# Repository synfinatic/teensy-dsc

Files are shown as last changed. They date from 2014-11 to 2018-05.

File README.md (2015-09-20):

# TeensyDSC: WiFi enabled Digital Setting Circles

## Important Note

As of Nov 16, 2014 I've been able to order a PCB from OSHPark using the 
[Simple-DSC](https://github.com/synfinatic/teensy-dsc/tree/simple-dsc/eagle)
design and with the latest code from 
[master](https://github.com/synfinatic/teensy-dsc/commit/1c4c6b0b567ba3cc21cd7ba83029384eee6130e7).
I seem to have a working solution using SkySafari Pro on my iPad with 
[US Digital S2-2500](http://www.usdigital.com/products/encoders/incremental/rotary/shaft/S2)
10,000 step optical encoders.

For more information, please see the [TeensyDSC Wiki](https://github.com/synfinatic/teensy-dsc/wiki)

There is also this thread on [CloudyNights](http://www.cloudynights.com/topic/482436-yet-another-diy-digital-setting-circles-project-teensydsc/)

## Basic Features
I wanted to do my own digital setting circles (DSC) for my 
[Apertura AD12](http://www.opticsmart.com/telescopes/dobsonian-telescopes/apertura-ad12-dobsonian-reflector-telescope.html).
The main goals were:

 * Tested to support 40,000 resolution via quadurature decoding using [US Digital S2-10000-250-IE-D-D encoders](http://usdigital.com/products/encoders/incremental/rotary/shaft/S2)
 * Should support resolutions in excess of 100K
 * Built in WiFi access point to allow wirelessly interfacing to an Apple iPad or Android tablet
 * Supporting at least [SkySafari Plus/Pro](http://www.skysafariastronomy.com/)
 * Powered via USB connection or external 7-24V battery source
 * Using industry standard RJ45 connection to encoders
 * Open source software & PCB design (GPLv3)
    * PCB Design done in [Eagle PCB](http://www.cadsoftusa.com/eagle-pcb-design-software/?language=en)
    * PCB's available from [OshPark](http://www.oshpark.com)
 * Small 2"x3"x1" enclosure
 * Inexpensive!  All the components should be available for < $100.

That will be version 1.0.  Future versions will hopefully support other features,
but for now that will be enough for it to work for me.

## Why Teensy 3.1
Why the [Teensy 3.1](http://pjrc.com/store/teensy31.html) and not Arduino?

 * It is *much* faster then the Arduino Uno or Mega (32bit 72Mhz CPU vs 16bit 16Mhz)
 * Small footprint and only costs $20!
 * Runs at 3.3V, but handles 5V just fine which simplifies talking to WiFi chipsets and encoders
 * It supports interrupts on all digital pins which allows for higher resolution encoders
 * Has 3 hardware serial ports which allows interfacing with GoTo hardware, etc
 * More memory & flash allows for a lot more features

## Required Libraries & Software
TeensyDSC requires some additional Arduino libraries to compile/run:

 * [Arduino IDE v1.6.x](http://arduino.cc/en/Main/Software)
 * [Teensyduino](http://pjrc.com/teensy/td_download.html) - Teensy addon for the Arduino IDE

The following libraries are included with the TeensyDSC source code, but you
will need to import them into the Arduino IDE:

 * [AnySerial](https://github.com/synfinatic/AnySerial) - Serial port abstraction layer for Arduino
 * [WiFi_Shield](https://github.com/synfinatic/WiFi_Shield) - Customized to use AnySerial
 * [Flash](https://github.com/mikalhart/Flash) - Easy access to EEPROM flash memory

## Supported DSC Software
Please note that I have limited access to software, so this may not be a
complete list.  If you have tested TeensyDSC with some software, I'd love
to hear if it worked or not.  If it did not work, hopefully we can work
together to make it work!

 * SkySafari (OSX, iOS)  
   * Scope Type: Basic Encoder System
   * For "Encoder Steps per Revolution" click "Get Automatically"

## Similar Projects
There are a bunch of similar projects to TeensyDSC which you should be aware of:

 * [mrosseel/arduino-dsc](https://github.com/mrosseel/arduino-dsc)
 * [mdw123/arduino-dsc](https://github.com/mdw123/arduino-dsc)
 * [Arduino Bluetooth DSC](http://orlygoingthirty.blogspot.com/2012/01/arduino-bluetooth-digital-setting.html)
 * [Mike Fulbright's Arduino DSC](http://msfastro.net/articles/arduinodsc/)

## Similar Commercial Products
There are two commercial products which shares many of the same features of TeensyDSC:

 * [Astro Devices Nexus](http://www.astrodevices.com/products/Nexus/Nexus.html)
 * [Dave Ek's Setting Circles](http://eksfiles.net/digital-setting-circles/)

## DSC to WiFi adapters
These commercial products connect your DSC adapter (Sky Commander, etc) to Sky Safari:

 * [Southern Stars/Orion SkyFi](http://www.southernstars.com/products/skyfi/)
 * [Astro Devices Nexus-S](http://www.astrodevices.com/products/NexusS/NexusS.html)

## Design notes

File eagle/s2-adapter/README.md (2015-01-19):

### US Digital S2 Adapter Board

This board makes it easy to connect a [US Digital S2 encoder](http://www.usdigital.com/products/encoders/incremental/rotary/shaft/S2) to your digital setting circles computer via a simple cable.  You will need an [RJ9 jack](http://www.digikey.com/product-search/en?KeyWords=A104907-ND&WT.z_header=search_go) for each board.

This board design is released under the [GPLv3](http://www.gnu.org/licenses/gpl-3.0.html).

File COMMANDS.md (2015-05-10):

# Supported Commands

## Basic DSC Mode (BDSC)

##### Decoder Key:
 * XXXXX = a five digit number in decimal format
 * [a|b] = "a" or "b"
 * [1-10] = Any value between 1 and 10 inclusive
 * \r = \<CR\> 
 * \t = \<TAB\>
 * \<some text\> = a variable length string like this description

#### Commands:
 * A
   * Returns: <nothing>
   * Action: Set aligned flag = True
 * a
   * Returns: Y or N
   * Action: Returns if the scope has been aligned or not
 * Q 
   * Returns: [+|-]XXXXX\t[+|-]XXXXX\r
   * Action: Get encoder DSC values (RA, DEC)
 * R XXXXX XXXXX\r
   * Returns: \<nothing\>
   * Action: Set encoder resolution (RA, DEC)
 * Z XXXXX XXXXX\r
   * Returns: *
   * Action: Set encoder resolution (RA, DEC)
 * G
   * Returns: [+|-]XXXXX\t[+|-]XXXXX\r
   * Action: Get encoder resolution (RA, DEC)
 * H
   * Returns: [+|-]XXXXX\t[+|-]XXXXX\r
   * Action: Get encoder resolution (RA, DEC)
 * V
   * Returns: \<version\>\r
   * Action: Get the software version of TeensyDSC
 * q
   * Returns: XXXXX\r
   * Action: Get the error count
 * T
   * Returns: XXXXX,XXXXX\r
   * Action: Toggle Test mode.  Prints encoder resolutions every 100ms
 * P
   * Returns: P
   * Action: Pretends to "power up" the encoders
 * MODE WIFI\r
   * Action: Switch to WiFly Command mode (see below)
 * MODE CONFIG\r
   * Action: Switch to TeensyDSC Command mode (see below)
 * MODE SERIAL\r
   * Action: Connect to Serial Port A
   
## WiFly Commands (MODE WIFI)
In this mode, most everything you type is passed directly to the WiFly chip.  In order to talk to it, you'll want to read the [WiFly User's Guide](http://dlnmh9ip6v2uc.cloudfront.net/datasheets/Wireless/WiFi/rn-wiflycr-ug-v1.2r.pdf).

Note, while in this mode the digital setting circiles (DSC) feature of the device will be unusable.

##### Warnings: 
 * Manually configuring your WiFly board may "brick" it and render it un-operable!
 * If you enter "command mode" ($$$), make sure you also exit command mode too! (exit)
 * Do not change the command to enter "command mode" as described in section 2.6.1 of the user manual!  Doing so will break TeensyDSC!

* EXIT\r
  * Action: Stop talking to the WiFly and return to the previous mode

## TeensyDSC Commands (MODE CONF)

#### WiFI Config commands
 * showconf\r
   * Action: prints the current TeensyDSC config
 * ssid \<ssid\>\r
   * Action: Changes the SSID of the AP
 * wpa [on|off]\r
   * Action: Enable/disable WPA security of the AP
 * wpa pass \<password\>\r
   * Action: Changes the WPA password of the AP
 * channel [1-13]\r
   * Action: Changes the WiFi channel of the AP
 * save\r
   * Action: Saves any WiFi changes to the AP EEPROM
 * reboot wifi\r
   * Resets the WiFly.  May be required for some changes to take effect!
 * reset defaults\r
   * Resets all the stored defaults in the TeensyDSC
 * EXIT\r
   * Action: Stop configuring the TeensyDSC and return to the previous mode

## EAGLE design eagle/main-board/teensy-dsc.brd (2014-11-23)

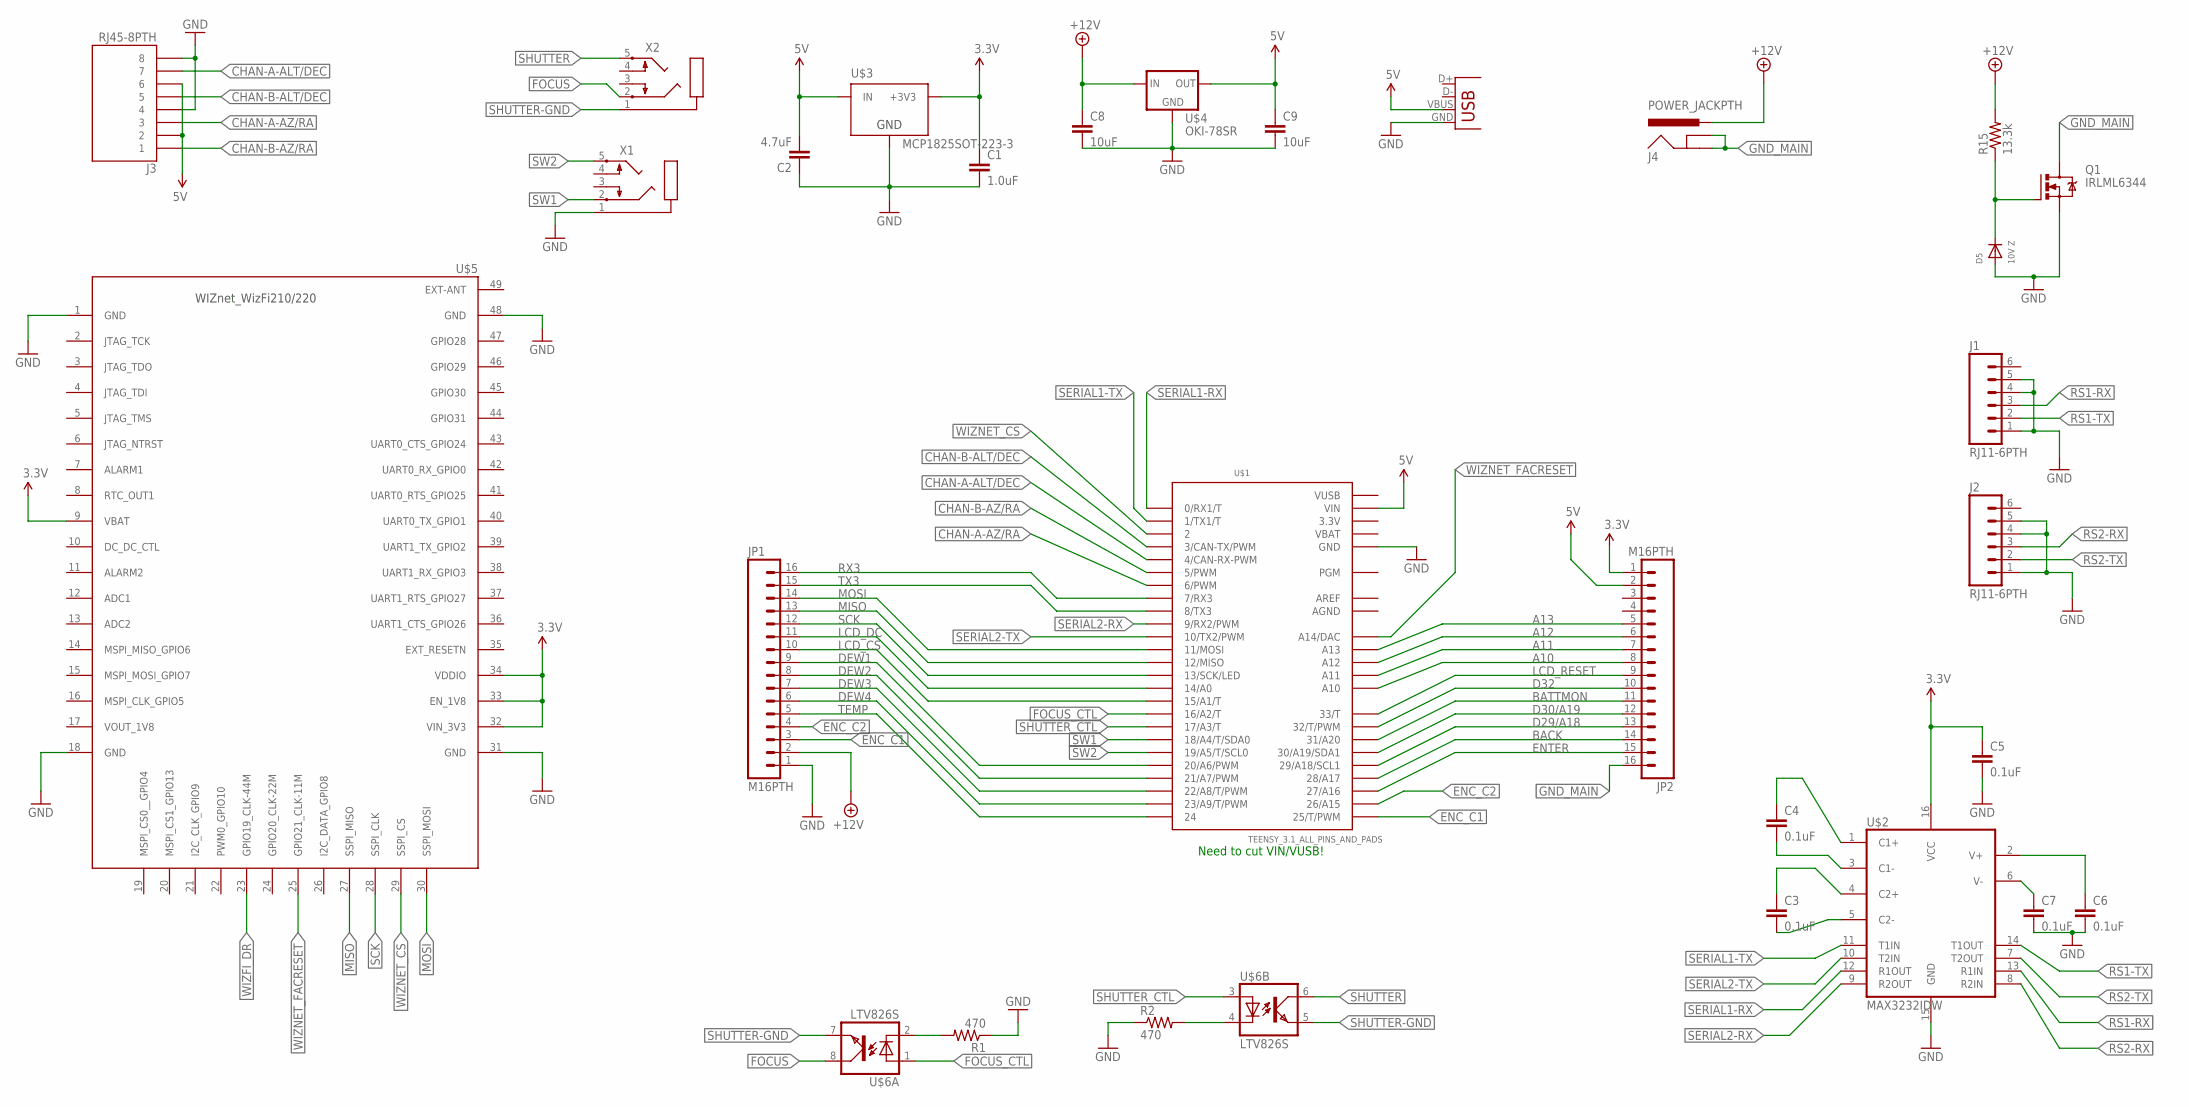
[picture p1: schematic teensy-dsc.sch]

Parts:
C1: 1.0uF; C0805
C2: 4.7uF; C0805
C3, C4, C5, C6, C7: 0.1uF; C0805
C8, C9: 10uF; C0805
D5: 10V Z; SOD-123
J1, J2: RJ11-6PTH; RJ11-6
J3: RJ45-8PTH; RJ45-8
J4: POWER_JACKPTH; POWER_JACK_PTH
J5: USB-B; USB-B-PTH
JP1, JP2: M16PTH; 1X16
Q1: IRLML6344; SOT23
R1, R2: 470; M0805
R15: 13.3k; M0805
U$1: TEENSY_3.1_ALL_PINS_AND_PADS; TEENSY_3.1_ALLPINS
U$2: MAX3232IDW; SO016
U$3: MCP1825SOT-223-3; SOT-223
U$4: OKI-78SR; OKI-78SR-H
U$5: WIZFI210/220
U$6: LTV826S; DIL8-SMD
X1, X2: STEREOJACK; STX3100

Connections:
3.3V: C1.1, C5.1, JP2.1, U$1.3.3V, U$1.3.3V1 (3.3V), U$1.3.3V2 (3.3V), U$2.16 (VCC), U$3.3 (+3V3), U$5.9 (VBAT), U$5.32 (VIN_3V3), U$5.33 (EN_1V8), U$5.34 (VDDIO)
5V: C2.2, C9.1, J3.2, J3.6, J5.VBUS, JP2.2, U$1.VIN, U$3.1 (IN), U$4.P$3 (OUT)
+12V: C8.1, J4.PWR, JP1.2, R15.2, U$4.P$1 (IN)
A10: JP2.8, U$1.A10
A11: JP2.7, U$1.A11
A12: JP2.6, U$1.A12
A13: JP2.5, U$1.A13
AGND: U$1.AGND
AREF: U$1.AREF
BACK: JP2.14, U$1.28 (28/A17)
BATTMON: JP2.11, U$1.31 (31/A20)
CHAN-A-ALT/DEC: J3.7, U$1.4 (4/CAN-RX-PWM)
CHAN-A-AZ/RA: J3.3, U$1.6 (6/PWM)
CHAN-B-ALT/DEC: J3.5, U$1.3 (3/CAN-TX/PWM)
CHAN-B-AZ/RA: J3.1, U$1.5 (5/PWM)
D29/A18: JP2.13, U$1.29 (29/A18/SCL1)
D30/A19: JP2.12, U$1.30 (30/A19/SDA1)
D32: JP2.10, U$1.32 (32/T/PWM)
DEW1: JP1.9, U$1.20/A6 (20/A6/PWM)
DEW2: JP1.8, U$1.21/A7 (21/A7/PWM)
DEW3: JP1.7, U$1.22/A8 (22/A8/T/PWM)
DEW4: JP1.6, U$1.23/A9 (23/A9/T/PWM)
ENC_C1: JP1.3, U$1.25 (25/T/PWM)
ENC_C2: JP1.4, U$1.26 (26/A15)
ENTER: JP2.15, U$1.27 (27/A16)
FOCUS: U$6.8 (COL), X2.2
FOCUS_CTL: U$1.16/A2 (16/A2/T), U$6.1 (A)
GND: C1.2, C2.1, C5.2, C6.2, C7.2, C8.2, C9.2, D5.A, J1.1, J1.4, J1.5, J2.1, J2.4, J2.5, J3.4, J3.8, J5.GND, JP1.1, Q1.2 (S), R1.1, R2.1, U$1.GND, U$1.GND1 (GND), U$1.GND2 (GND), U$2.15 (GND), U$3.2 (GND), U$4.P$2 (GND), U$5.1 (GND), U$5.18 (GND), U$5.31 (GND), U$5.48 (GND), X1.1
GND_MAIN: J4.GND, J4.GNDBREAK, JP2.16, Q1.3 (D)
LCD_CS: JP1.10, U$1.15/A1 (15/A1/T)
LCD_DC: JP1.11, U$1.14/A0
LCD_RESET: JP2.9, U$1.33 (33/T)
MISO: JP1.13, U$1.12 (12/MISO), U$5.27 (SSPI_MISO)
MOSI: JP1.14, U$1.11 (11/MOSI), U$5.30 (SSPI_MOSI)
unnamed: C4.1, U$2.1 (C1+)
unnamed: C4.2, U$2.3 (C1-)
unnamed: C3.1, U$2.4 (C2+)
unnamed: C3.2, U$2.5 (C2-)
unnamed: C7.1, U$2.6 (V-)
unnamed: C6.1, U$2.2 (V+)
unnamed: R2.2, U$6.4 (C)
unnamed: R1.2, U$6.2 (C)
unnamed: D5.C, Q1.1 (G), R15.1
RS1-RX: J1.3, U$2.13 (R1IN)
RS1-TX: J1.2, U$2.14 (T1OUT)
RS2-RX: J2.3, U$2.8 (R2IN)
RS2-TX: J2.2, U$2.7 (T2OUT)
RX3: JP1.16, U$1.7 (7/RX3)
SCK: JP1.12, U$1.13 (13/SCK/LED), U$5.28 (SSPI_CLK)
SERIAL1-RX: U$1.0 (0/RX1/T), U$2.12 (R1OUT)
SERIAL1-TX: U$1.1 (1/TX1/T), U$2.11 (T1IN)
SERIAL2-RX: U$1.9 (9/RX2/PWM), U$2.9 (R2OUT)
SERIAL2-TX: U$1.10 (10/TX2/PWM), U$2.10 (T2IN)
SHUTTER: U$6.6 (COL), X2.5
SHUTTER-GND: U$6.5 (EMIT), U$6.7 (EMIT), X2.1
SHUTTER_CTL: U$1.17/A3 (17/A3/T), U$6.3 (A)
SW1: U$1.18/A4 (18/A4/T/SDA0), X1.2
SW2: U$1.19/A5 (19/A5/T/SCL0), X1.5
TEMP: JP1.5, U$1.24
TX3: JP1.15, U$1.8 (8/TX3)
VBAT: U$1.VBAT
VUSB: U$1.VUSB
WIZFI_DR: U$5.23 (GPIO19_CLK-44M)
WIZNET_CS: U$1.2, U$5.29 (SSPI_CS)
WIZNET_FACRESET: U$1.A14 (A14/DAC), U$5.25 (GPIO21_CLK-11M)

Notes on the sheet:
Need to cut VIN/VUSB!

Board: 2 copper layers, 29 parts (17 on the bottom side), 60 nets, no tracks yet.

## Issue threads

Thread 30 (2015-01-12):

Create Youtube video of how to install & configure the software

synfinatic, 2015-01-12:
Should create 2 videos:

1. Install software on the TeensyDSC via the Arduino App
2. Configure the TeensyDSC for your encoders/network/iPad

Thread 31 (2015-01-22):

Add support for Orion Intelliscope encoders

synfinatic, 2015-01-22:
It looks like it would be possible to support Orion Intelliscope encoders.  Basically they generate a two channel analog signal which is decoded very much like quadrature decoding for digital encoders, but rather then 'ticks' we have 32 magnetic zones.  [More info here](http://maxwell.fief.org/intelliscope.html)

Support would require:
 1. Supporting analog input for the encoders
 2. The encoders generate a .2->4.7V analog signal.  So we'd need to convert that to 0->3.3V
 3. Write the code to support it.

Obviously item 2 is the biggest issue here.  Probably the best solution is an off-board ADC which supports 5V.

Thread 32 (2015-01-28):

OKI module doesn't fit in 0.5.3 board

synfinatic, 2015-01-28:
The pins on the OKI power module are a larger diameter then the holes in the board.  Need to increase drill hole size so they fit.

synfinatic, 2015-01-28:
Fixed in v0.5.4

Closed 2015-01-28.

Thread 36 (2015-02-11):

Switch to QuadEncoder library

synfinatic, 2015-02-11:
Teensy 3.1 has specific hardware support for quadrature decoding of up to 2 encoders.  Should provide even better performance then the interrupt driven mode.

http://forum.pjrc.com/threads/26803-Hardware-Quadrature-Code-for-Teensy-3-x

synfinatic, 2015-02-13:
Will require a hardware change as the pins for the hardware decoding requires specific pins:
 *    ENCXA	 3
 *    ENCXB	 4
 *    ENCYA	32
 *    ENCYB	25

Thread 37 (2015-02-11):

Account for mount errors

synfinatic, 2015-02-11:
Basically, add intelligence to TeensyDSC so we can account for mount errors where the scope doesn't rotate perfectly about the encoder axis. Not really sure how I'd go about this, but I'm sure it's technically possible.

http://www.cloudynights.com/topic/482436-yet-another-diy-digital-setting-circles-project-teensydsc/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

synfinatic, 2015-04-27:
Basically I'd have to emulate a SkyCommander ala #7.  Perhaps not so crazy after all?

Closed 2015-04-27.

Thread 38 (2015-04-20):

SkySafari hangs for ~1sec

synfinatic, 2015-04-20:
While using SkySafari with the TeensyDSC, it has been known to happen that SkySafari sometimes stops updating it's screen.  Currently, it's unknown if this is a SkySafari issue, WiFi communication issue or an issue with TeensyDSC.

I should write a script which acts like SkySafari and see if I can reproduce the issue.

synfinatic, 2015-05-10:
I wrote the script and I'm really having a difficult time reproducing the problem.  It appears to be more SkySafari/iPad related right now.  More research required

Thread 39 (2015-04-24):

Encoder counters are wrong?

synfinatic, 2015-04-24:
So it appears that while the current code works fine with SkySafari, that's because it's willing to accept invalid values.  Honestly, it's hard to really tell since the specs are so badly written, but the best written spec (for the MicroGuider5) clearly shows that min/max range should be +/- 1/2 the encoder resolution.  Ie: for a 4000 tick encoder, -2000 to +1999 are valid.

The caveat is that for resolutions > 2^16 (like my 40000) tick encoders, then you'd use a range of 0-39999.  Clearly, they are using a 16bit integer for storage!

Right now the biggest challenge is testing... Trying to find some free non-SkySafari software which actually has the limitation for testing.

Closed 2015-05-06.

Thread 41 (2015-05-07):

Rework project to include libraries in source tree

synfinatic, 2015-05-07:
Having to manually import & include a bunch of libraries suck.  Looks like there is a solution like documented here:
http://stackoverflow.com/questions/4705790/keeping-all-libraries-in-the-arduino-sketch-directory

synfinatic, 2015-05-11:
So those directions on having a "libraries" directory didn't work as described.  So for now, I've just done gitremote's for the libraries so it's included in tarball/clone.  The next best solution is to create a custom Makefile I guess???  Challenging to make it crossplatform though. :-/

Closed 2015-05-11.

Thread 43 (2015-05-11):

Build code using included libraries

synfinatic, 2015-05-11:
Would be nice to not have to install the libraries included in Git.  Not sure how to solve this problem because the Arduino IDE is really really stupid when it comes to CPP includes and libraries.   A good starting point is this thread:

https://forum.pjrc.com/threads/28393-Recommended-software-for-building-Teensy-projects-on-the-command-line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

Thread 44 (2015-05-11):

Improve WiFly config CLI

synfinatic, 2015-05-11:
Right now, configuring the WiFly is a PITA.  Things should be easier for users to configure and the config in the Teensy should reflect that of the WiFly module.  I'm not even sure a "save" command is required?  Definitely should have a "reset to factory defaults" option though.

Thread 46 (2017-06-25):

Negative encoder resolutions are broken

synfinatic, 2017-06-25:
Not sure what is going on really, but twice now I've driven 90min to Pinnacles NP and then found the config on the Teensy seems to have been corrupted and the result is the Alt encoder resolution is wrong.  Since I can't _set_ the resolution via Telnet/SkySafari I've been SOL (guess I should bring a laptop & usb cable???).

synfinatic, 2017-06-30:
More in-depth analysis shows that it's a software bug.  Specific bug is when resolution is negative.   Impacts encoders of all resolutions.

synfinatic, 2017-07-09:
Tried it on my scope last night and it still didn't work. :(

Closed 2017-07-09.

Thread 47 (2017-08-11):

RN-XV not getting configured

BVIS222, 2017-08-11:
Hi Aaron,
I've been trying to get your hardware setup and code running on a breadboarded version of your DSC. It compiles, it reads the encoders, but it is not configuring the RN-XV with the network settings. It is just defaulting to WiFly-EZX-a9 with the default IP address of 192.168.1.1. I've used a printout from eagle of your board to figure out what pins go where but I may be missing something.
I'm doing this on a bread board to get it working first and then it will go into the box with my scope drive system. There is very little room left in the box so building it on your PCB is not really an option.
Any help you can give me would be greatly appreciated.

My email address is bvis222@yaoo.com. This will be easier then using GitHub to communicate ... but that's up to you.

Craig

synfinatic, 2017-08-11:
Have you read the instructions here? https://github.com/synfinatic/teensy-dsc/wiki/Manual-0.5.x

It explains the CLI commands to configure the WiFi

BVIS222, 2017-08-11:
Thanks for getting back to me so fast...
I've tried that again and it does load the info into the eprom but it never uses that data to change the rn-xv to that ssid or ip address. I'm probably not doing something correctly. Could it be that the RN-XV firmware is causing this....version is 4.41.
Craig 

      From: Aaron Turner <notifications@github.com>
 To: synfinatic/teensy-dsc <teensy-dsc@noreply.github.com>
Cc: BVIS222 <BVIS222@YAHOO.COM>; Author <author@noreply.github.com>
 Sent: Friday, August 11, 2017 10:54 AM
 Subject: Re: [synfinatic/teensy-dsc] RN-XV not getting configured (#47)

Have you read the instructions here? https://github.com/synfinatic/teensy-dsc/wiki/Manual-0.5.xIt explains the CLI commands to configure the WiFi—
You are receiving this because you authored the thread.
Reply to this email directly, view it on GitHub, or mute the thread.

synfinatic, 2017-08-11:
What commands are you using to configure the WiFly?

BVIS222, 2017-08-11:
SET SSID SCOPEDOG => Set the WiFi SSID
SET PASS SCOPEDOG => Set the WiFi passphrase
SET IP 10.0.0.1 => Set the WiFi IP address
SET MASK 255.255.255.0 => Set the WiFi netmask
SET CHAN 4 => Set the WiFi channel [0-12]
SET PORT 4030 => Set the TCP PORT [1-65535]
SET RATE 2 => Set the WiFi rate [0-15]
SET TXP 12 => Set the WiFi TX Power [0-12]
SET AUTH OPEN         => Enable WPA2-PSK or no security
SET MODE AP             => Enable AP or client mode
SET ALT 1440 => set ALT encoder resolution
SET AZ 1440 => set AZ encoder resolution
SAVE
GET ALL returns:
SSID: ScopeDog
PASS: scopedog
IP: 10.0.0.1
MASK: 255.255.255.0
CHAN: 4
PORT: 4030
AUTH: OPEN
MODE: AP
RATE: 2
TXP: 12
ALT/Dec: 1440
AZ/RA: 1440
Then MODE DSC to get back to DSC modeThen I look at WiFi list on computer and all I see is WiFly-EZX-a9Cycle power
Then I look at WiFi list on computer and all I see is WiFly-EZX-a9

From: Aaron Turner <notifications@github.com>

 To: synfinatic/teensy-dsc <teensy-dsc@noreply.github.com>
Cc: BVIS222 <BVIS222@YAHOO.COM>; Author <author@noreply.github.com>
 Sent: Friday, August 11, 2017 1:14 PM
 Subject: Re: [synfinatic/teensy-dsc] RN-XV not getting configured (#47)

What commands are you using to configure the WiFly?—
You are receiving this because you authored the thread.
Reply to this email directly, view it on GitHub, or mute the thread.

BVIS222, 2017-08-11:
I got it workingI need to do and AP SAVE to get it
Thanks for the help.
Will now try and connect via SkySafari

      From: Aaron Turner <notifications@github.com>
 To: synfinatic/teensy-dsc <teensy-dsc@noreply.github.com>
Cc: BVIS222 <BVIS222@YAHOO.COM>; Author <author@noreply.github.com>
 Sent: Friday, August 11, 2017 1:14 PM
 Subject: Re: [synfinatic/teensy-dsc] RN-XV not getting configured (#47)

What commands are you using to configure the WiFly?—
You are receiving this because you authored the thread.
Reply to this email directly, view it on GitHub, or mute the thread.

synfinatic, 2017-08-11:
Yep, I was just about to mention AP SAVE. 👍

Closed 2017-08-11.

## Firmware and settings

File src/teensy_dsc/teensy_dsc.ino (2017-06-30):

/*
 * Teensy 3.1 Digital Setting Circles
 * Copyright (C) 2014-2015 Aaron Turner
 *
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
 */

#include <Arduino.h>
#define ENCODER_OPTIMIZE_INTERRUPTS
#include <Encoder.h>
#include <AnySerial.h>
#include <WiFly.h>
#include <Flash.h>
#include <MsTimer2.h>

#include "defaults.h"
#include "teensy_dsc.h"
#include "rnxv.h"
#include "utils.h"
#include "cli.h"
#include "defaults.h"


/*
 * Init our Encoders & Serial ports
 */
Encoder EncoderRA(CHAN_A_RA, CHAN_B_RA);
Encoder EncoderDEC(CHAN_A_DEC, CHAN_B_DEC);

AnySerial UserSerial(&USER_SERIAL_PORT);
AnySerial WiFlySerialPort(&WIFLY_SERIAL_PORT);
WiFly _WiFly(WiFlySerialPort);
cmd_status process_cmd(cli_ctx *ctx);

/* our global contexts */
cli_ctx *uctx, *wctx;
common_cli_ctx *common;
uint32_t test_mode_wait;

/* blink our LED */
void
blink_led() {
    static int onoff = 0;
    onoff = onoff == 1 ? 0 : 1;
    digitalWrite(BLINK_LED, onoff);
}



void
setup() {
    pinMode(WIFLY_RESET, INPUT);
    pinMode(BLINK_LED, OUTPUT);
    encoder_settings_t *encoders;
    serial_settings_t *serial;
    float ver;

    test_mode_wait = 0;

    digitalWrite(BLINK_LED, HIGH);
    UserSerial.begin(USER_SERIAL_SPEED);
    pinMode(WIFLY_RESET, INPUT);

    common = (common_cli_ctx *)malloc(sizeof(common_cli_ctx));

    serial = get_serial_settings();
    WiFlySerialPort.begin(serial->wifly_baud);

    delay(1000);

    // load the encoder settings stored in the EEPROM
    encoders = get_encoder_settings();
    common->ra_cps = encoders->ra_cps;
    common->dec_cps = encoders->dec_cps;
    common->network = get_network_settings();

    // Init the USB Serial port & context
    UserSerial.printf("Waiting %ums for WiFly...\n", WIFLY_DELAY);
    // Init the WiFly
    delay(WIFLY_DELAY);   // Wait for it to come up

    UserSerial.print("WiFly Version: ");
    ver = _WiFly.version();
    UserSerial.println(ver);
    if (ver < 2.45) {
        Serial.println("Warning! The WiFly's firmware probably doesn't support AP mode.");
        Serial.println("Update the WiFly's firmware with wifly_update example");
    }

    UserSerial.printf("Initializing CLI's...");
    wctx = cli_init_cmd(&WiFlySerialPort, common, NULL, &EncoderRA, &EncoderDEC);
    uctx = cli_init_cmd(&UserSerial, common, &_WiFly, &EncoderRA, &EncoderDEC);
    UserSerial.printf("  OK!\n");

    // Debug mode
    if (common->network->debug_wifly) {
        WiFlySerialPort.attach_debug(&UserSerial);
        WiFlySerialPort.debug(1);
    }

    // don't need this anymore
    free(serial);
    free(encoders);

    // Start reading the encoders
    MsTimer2::set(BLINK_LED_MS, blink_led);
    MsTimer2::start();

}


void
loop() {
    uint32_t now = millis();
    if (UserSerial.available() > 0) {
        process_cmd(uctx);
    }

    if (_WiFly.available() > 0) {
        process_cmd(wctx);
    }

    if (uctx->common->test_mode && test_mode_wait <= now) {
        dsc_get_values(uctx, NULL);
        test_mode_wait = now + TEST_MODE_DELAY;
    }
}

/*
 * Reads from *serial and trys to execute the given command.
 * 
 * Returns a cmd_status based on if we ran a command
 */
cmd_status
process_cmd(cli_ctx *ctx) {
    AnySerial *serial = ctx->serial;
    static char read_buff[READBUFF_SIZE];
    static size_t pos = 0;
    char temp_buff[READBUFF_SIZE], byte;
    size_t i, len;
    cmd_status status;

    // Short cut for one char commands
    if (pos == 0) {
        i = 0;
        byte = serial->peek();
        while (ctx->one_char_cmds[i] != '\0') {
            if (byte == ctx->one_char_cmds[i]) {
                read_buff[0] = byte;
                read_buff[1] = '\0';
                status = cli_proc_cmd(ctx, read_buff, 1);
                serial->read(); // consume the byte 
                read_buff[0] = '\0';
                return status;
            }
            i++;
        }
    }

    /*
     * Command is multiple bytes followed by '\r'
     */
    len = serial->readBytesUntil('\r', temp_buff, READBUFF_SIZE);
    if (((strlen(read_buff) + len) > READBUFF_SIZE) ||
        (len == READBUFF_SIZE)) {
        // Crap, someone is just sending us crap.  Just eat it.
        pos = 0;
        read_buff[0] = '\0';
        return E_CMD_TOO_LONG;
    }

    // append the last bytes to any bytes we've read before
    strcat(read_buff, temp_buff);
    pos = strlen(read_buff);


    // trim any whitespace on the end
    if (IS_WORD_END(read_buff[len-1])) {
        while (IS_WORD_END(read_buff[len-1])) {
            read_buff[len-1] = '\0';
        }
    } 

    if (strlen(read_buff) == 0) {
        return E_CMD_TOO_SHORT;
    }

    // At this point we should have a whole command.  Go process it!
    status = cli_proc_cmd(ctx, read_buff, strlen(read_buff));

    switch (status) {
        case E_CMD_TOO_LONG:
        case E_CMD_NOT_FOUND:
        case E_CMD_BAD_ARGS:
#ifdef DEBUG
            if (! ctx->eat_errors) {
                serial->printf("ERR [%d]: %s\n", status, read_buff);
            }
#endif
            // fall through
            pos = 0;
            read_buff[0] = '\0';
            break;
        case E_CMD_OK:
            // Eat what we've been given and return
            pos = 0;
            read_buff[0] = '\0';
            break;
        case E_CMD_TOO_SHORT:
            // Keep the buffer for next time 
            break;
    }
    return status;
}


/*
 * Resets the WiFly
 */
void
reset_wifly() {
    UserSerial.write("\nResetting the Xbee...  ");
    pinMode(WIFLY_RESET, OUTPUT);
    digitalWrite(WIFLY_RESET, LOW);
    delay(100);
    pinMode(WIFLY_RESET, INPUT);
    UserSerial.write("Done!\n");
}

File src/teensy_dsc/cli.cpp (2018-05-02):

/*
 * Teensy 3.1 Digital Setting Circles
 * Copyright (C) 2014-2015 Aaron Turner
 *
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
 */

#include <Arduino.h>
#include <AnySerial.h>
#include "teensy_dsc.h"
#include "cli.h"
#include "utils.h"
#include "defaults.h"
#include "rnxv.h"
#include "dsc.h"

void setup_commands(cli_ctx *ctx);

/*
 * Initalizer for a CLI context
 */
cli_ctx *
cli_init_cmd(AnySerial *aserial, common_cli_ctx *common, WiFly *wifly,
        Encoder *ra, Encoder *dec) {
    cli_ctx *ctx;

    ctx = (cli_ctx *)malloc(sizeof(cli_ctx));
    memset(ctx, 0, sizeof(cli_ctx));
    ctx->common = common;
    ctx->common->test_mode = false;
    ctx->common->alignment = false;
    ctx->state = BASIC_DSC;
    ctx->prev_state = NONE;
    ctx->serial = aserial;
    ctx->wifly = wifly;
    ctx->ra = ra;
    ctx->dec = dec;
    if (wifly == NULL) {
        ctx->eat_errors = true;
    } else {
        ctx->eat_errors = false;
    }
    setup_commands(ctx);

    return ctx;
}

/*
 * Run this every time we change CLI state
 * to update our CTX
 */
void
change_state(cli_ctx *ctx, cli_state new_state) {
    ctx->prev_state = ctx->state;
    ctx->state = new_state;

    setup_commands(ctx);

    // if changing to WIFI mode, then enter now.
    if (ctx->state == WIFI && ctx->wifly != NULL) {
        wifi_interactive(ctx);
    } else if (ctx->state == WIFI) {
        ctx->serial->printf("ctx->wifly not defined. Can't change mode\n");
        ctx->state = ctx->prev_state;
        setup_commands(ctx);
    } else {
        ctx->serial->printf("OK\n");
    }
}

/*
 * Parse the line and execute the given command.
 *
 * Returns true/false depending on if the cmd line
 * passed in was successfully processed and can
 * be freed by the caller
 *
 * TODO: Handle commands of any size more gracefully
 * by actually using the len option
 */
cmd_status
cli_proc_cmd(cli_ctx *ctx, char *line, size_t len) {
    char cmd[READBUFF_SIZE];
    char args[READBUFF_SIZE], byte, *line2;
    size_t pos = 0, line_max;
    bool has_args = false;

    cmd[0] = '\0';
    args[0] = '\0';

    /* split the line into the cmd & args */
    byte = line[0];
    line_max = strlen(line);
    while ((! IS_WORD_END(byte)) && (pos < line_max)) {
        pos ++;
        byte = line[pos];
    }
    if (IS_WORD_END(line[pos])) {
        line[pos] = '\0';
        line2 = &(line[pos+1]);
        strncpy(args, line2, 254);
        has_args = true;
    }
    strncpy(cmd, line, (READBUFF_SIZE-1));

    /* execute the cmd based on the current context */
    pos = 0;
    while (COMMANDS[pos].state != NONE) {
        if ((COMMANDS[pos].state == ctx->state) &&
                (strcmp(COMMANDS[pos].cmd, cmd) == 0) && 
                (COMMANDS[pos].has_args == has_args)) {
            return COMMANDS[pos].fh(ctx, args);
        }
        pos++;
    }
    return E_CMD_NOT_FOUND;
}

/*
 * Prints the current encoder values
 *
 * each value is signed 6 values, delimited by a tab and 
 * terminted with a \r
 */
cmd_status
dsc_get_values(cli_ctx *ctx, const char *args) {
    char buff[36];
    char *value;
    int32_t ra, dec;

    ra = ctx->ra->read();
    dec = ctx->dec->read();

    ra = ngc_convert_encoder_value(ra, ctx->common->ra_cps);
    dec = ngc_convert_encoder_value(dec, ctx->common->dec_cps);

    value = EncoderValue(ra, true);
    sprintf(buff, "%s\t", value);
    value = EncoderValue(dec, true);
    strcat(buff, value);
    ctx->serial->printf("%s\r\n", buff);
    return E_CMD_OK;
}


/*
 * Allows the user to set the Encoder resolution
 */
cmd_status
dsc_set_resolution(cli_ctx *ctx, const char *args) {
    int match = 0;
    long ra, dec;
    encoder_settings_t encoder_settings;

    /* there may be a \r\n here to parse as well??? */
    match = sscanf(args, "%ld %ld", &ra, &dec);
    if (match != 2) {
        return E_CMD_TOO_SHORT;
    }

    ctx->common->ra_cps = ra;
    ctx->common->dec_cps = dec;
    ctx->common->alignment = false;

    /* write the values to EEPROM for later */
    encoder_settings.ra_cps = ctx->common->ra_cps;
    encoder_settings.dec_cps = ctx->common->dec_cps;
    set_encoder_settings(&encoder_settings);
    return E_CMD_OK;
}

/*
 * Toggle test mode on/off
 */
cmd_status
dsc_test_mode(cli_ctx *ctx, const char *args) {
    // flip the bit
    ctx->common->test_mode = ctx->common->test_mode ? false : true;
    return E_CMD_OK;
}

/*
 * BBox set encoder resolution
 */
cmd_status
bbx_set_resolution(cli_ctx *ctx, const char *args) {
    dsc_set_resolution(ctx, args);
    ctx->serial->printf("*");
    return E_CMD_OK;
}

/*
 * BBox get status
 */
cmd_status
bbx_get_status(cli_ctx *ctx, const char *args) {
    // no errors, battery OK
    ctx->serial->printf("001\r\n");
    return E_CMD_OK;
}
 
/*
 * prints the current encoder resolution
 */
cmd_status
dsc_get_resolution(cli_ctx *ctx, const char *args) {
    long ra, dec;
    char ra_pos[2], dec_pos[2];

    ra = abs(ctx->common->ra_cps);
    dec = abs(ctx->common->dec_cps);

    ra_pos[1] = dec_pos[1] = '\0';
    ra_pos[0] = ra == ctx->common->ra_cps ? '+' : '-';
    dec_pos[0] = dec == ctx->common->dec_cps ? '+' : '-';

    ctx->serial->printf("%s%05ld\t%s%05ld\r\n", ra_pos, ra, dec_pos, dec);
    return E_CMD_OK;
}

/*
 * TeensyDSC software version
 */
cmd_status
dsc_get_version(cli_ctx *ctx, const char *args) {
    ctx->serial->printf("%s\n", TEENSY_DSC_VERSION); 
    return E_CMD_OK;
}

/*
 * Change the current CLI state
 */
cmd_status
change_cli_state(cli_ctx *ctx, const char *args) {
    int mode = 0;
    cli_state new_state = NONE;

    while (MODES[mode].state != NONE) {
        if (strcmp(MODES[mode].name, args) == 0) {
            new_state = MODES[mode].state;
        }
        mode ++;
    }

    if (new_state != NONE) {
        if (new_state != ctx->state) {

            // Don't let people reconfigure things over wireless
            if ((new_state == WIFI || new_state == CONFIG) &&
                    ctx->wifly == NULL) {
                ctx->serial->printf("Sorry, this is not available via wireless\n");
                return E_CMD_BAD_ARGS;
            }

            change_state(ctx, new_state);
        }
        return E_CMD_OK;
    }
    return E_CMD_BAD_ARGS;
}

cmd_status
dsc_get_help(cli_ctx *ctx, const char *args) {

    ctx->serial->printf(F("\n" \
"A                      => set alignment\n" \
"a                      => get alignment\n" \
"Q                      => get encoder values\n" \
"R xxxx xxxx            => set encoder resolution\n" \
"Z +xxxxx +xxxxx        => set encoder resolution (BBox)\n" \
"G                      => get encoder resolution\n" \
"H                      => get encoder resolution (BBox)\n" \
"V                      => get TeensyDSC version\n" \
"P                      => get status (BBox)\n" \
"T                      => Toggle Test Mode\n" \
"?                      => Help\n" \
"MODE [WIFI|CONFIG]     => change CLI mode\n"));

    return E_CMD_OK;
}
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

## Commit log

2014-09-08 First pass at a working board Teensy DSC
    - Power via USB cable
    - DSC uses same RJ45 pintout as AstroDevices Nexus
    - Uses Teensy 3.1 & any valid Xbee module!
    [teensy-dsc.brd, teensy-dsc.sch]
2014-09-08 updated with:
    - latest WiFly board
    - Thicker traces for routing 5V & GND
    - Removed wiring for 3.3V on Teensy 3.1 board
    [teensy-dsc.brd, teensy-dsc.sch]
2014-09-09 New board design: - Add 2x serial ports - Add camera trigger (opto-isolated) - Add 2x external button/switch - Add dedicated program button Remove old PCB design files Start work on TeensyDSC code
    [teensy-dsc.brd, teensy-dsc.sch]
2014-09-09 Mark board v0.2 Add a warning so people don't think it's ready for prime-time.
    [teensy-dsc.brd, teensy-dsc.sch]
2014-09-10 update README & don't track the Eagle .pro files
2014-09-10 Update board design with: - Remove program button since USB host mode isn't supported - Add 5mm barrel connector for ~12V power - Add necessary reverse polarity protection & regulation for 12V power 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
    [teensy-dsc.brd, teensy-dsc.sch]
2014-09-11 We don't need digitalWriteFast on the Teensy
2014-09-12 rename directory/files so Arduino app will open them- doesn't like dashes in file name :-/
    [defaults.h, defaults.ino, teensy_dsc.h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]
2014-09-13 Fix power error in .sch Update board to theoretically fit in CU-789 box
    [teensy-dsc.brd, teensy-dsc.sch]
2014-09-13 fix labels on board
    [teensy-dsc.brd]
2014-09-14 sync up with latest board change v0.4
2014-09-14 Lots of bug changes. teensy_dsc.ino currently uses AnySerial
    [defaults.ino, teensy_dsc.h, teensy_dsc.ino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]
2014-09-14 fix compile time warnings
    [defaults.ino, teensy_dsc.ino]
2014-09-14 Add support for SoftwareSerial (aka NewSoftSerial) Add support for print/printf/etc to AnySerial update teensy_dsc & wifly to use updated AnySerial code
2014-09-14 remove unneeded code & small cleanup for teensy_dsc
2014-09-15 Lots of changes:
    - Start working on a CLI framework
    - Update Commands & Readme docs
    - Note on the Eagle file that we need to cut the VUSB/VIN pads apart
    - Re-organize some header files
    - general cleanup
    [teensy-dsc.sch]
2014-09-16 rework inital WiFly setup
    - put static strings in Flash
    - clean up constants
    [cli.cpp, defaults.h, teensy_dsc.ino]
2014-09-20 lots of changes:
    - Defaults are now written to EEPROM
    - Config params are passed into WiFlySerial via API rather the CLI
    - CLI now handles it's own context
    - Much better error handling in CLI
    - use MsTimer2 to update encoders
    [cli.cpp, defaults.h, defaults.ino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]
2014-09-20 Basic CLI encoder reading & setting of resolution seems to be working
    Still need to apply resolution some how??
2014-09-22 extend CLI a lot and add support for WiFi
    - saving network/etc options to EEPROM now works
    - reading from EEPROM works
    - Some WiFi config works (SSID does NOT work??)
    - Enabling AP mode does not work (hangs)
    - remove a lot of unneeded debug statements
    - WiFi interactive (talking directly with WiFly board) works
    [cli.cpp, defaults.h, teensy_dsc.h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]
2014-11-17 Orion Intelliscope mode with SkySafari Pro 4.0 works!
    - Tested AP mode
    - Able to configure WiFly board & save settings
    - Switched from WiFlySerial to WiFly library
2014-11-19 don't track eagle/eagle.epf
2014-11-19 link to CN thread
2014-11-21 Start v0.9 board design
    - Has two 1x16 headers for expansion boards
    - 85x55mm design
    - four mounting holes
    - ports on two sides
    [teensy-dsc.brd, teensy-dsc.sch]
2014-11-21 approve DRU rule check
    [teensy-dsc.sch]
2014-11-22 move teensy-dsc design to main-board
    Last design with WiFly board
    [teensy-dsc.brd, teensy-dsc.sch]
2014-11-22 Initial WizFi210/220 redesign
    Also fixes naming of various Teensy pins which were wrong
    or incorrectly routed for serial ports/shutter/focus per
    the Google doc.
    [teensy-dsc.brd, teensy-dsc.sch]
2014-11-22 start work on dew-heater board & remove root dir DESCRIPTION
    [dew-heater.sch]
2014-11-23 more WizFi updates....
    After further research, I'm not convinced the WizFi is the way to go.
    Most likely will need to replace it with something else if I want
    to support serial ports. Probably should move the serial ports
    to a daughter board.
    [teensy-dsc.brd, teensy-dsc.sch]
2014-11-25 Massive fixes to EEPROM defaults saving & loading.
    Reflashing always zeros out the EEPROM. We now load
    our defaults from defaults.h if needed. Once you change
    the config, call SAVE and they'll be stored in the EEPROM
    until the next time you reflash the code.
    Most if not all the config options are now properly set & read.
    [cli.cpp, defaults.h, defaults.ino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]
2014-11-30 stop using MsTimer2 to update encoders, just read as needed
2014-11-30 move printf strings to flash via F()
2014-11-30 fix MODE WIFI mode
    Less confusing now. Auto passes '$$$' to the WiFly and 'exit\r'
    when we change modes.
    refs #28
    [cli.cpp]
2014-11-30 reintroduce LED blinking to indicate all is OK
    During startup, the LED is solid on and starts blinking
    once we're ready
2015-01-18 fix some bugs with the CLI:
    - Not saving encoder values in EEPROM
    - Can't switch to AP mode
    - Memory is reused w/o zero'd out
    [cli.cpp]
2015-01-19 add S2 Adapter breakout board v1.0
    [s2-adapter.brd, s2-adapter.sch]
2015-01-19 Add a short readme about the S2 adapter board
2015-01-29 fix setting AP SSID on WiFly
    [rnxv.ino]
2015-02-04 fix compile warnings and some small bugs
    [defaults.ino, rnxv.ino]
2015-03-20 add support for BBox Z, H and P cli commands fix compile warnings
    fixes #34
    [cli.cpp, defaults.ino]
2015-04-09 update readme with latest info on SkySafari modes and Arduino software version
2015-04-25 Ticket #39: Fix encoder readout
    Change code to match the spec as provided by the MicroGuider.
    We now wrap between +/- half resolution for resolution <= 2^16
    or 0->resolution-1 for higher resolutions.
    [cli.cpp, utils.ino]
2015-05-01 first pass at adding some unit tests.
    many tests fail, but at least I have something to work with.
    [unit_tests.ino]
2015-05-06 Fix #39: Fix ngc_convert_encoder_value()
    Unit tests seem to work and cover all our corner cases
    Update teensy_dsc code to use fixed method
    Still, wish I didn't have to duplicate the code. :-/
    [unit_tests.ino, utils.ino]
2015-05-07 ticket #40: Add test mode
    Press T to toggle between test mode on & off.
    Right now it's hard coded to print every 100ms.
2015-05-08 add simple test.py script for testing TeensyDSC
2015-05-08 fixes #42: alignment support
    adds support for the A and a commands to track alignment
    [cli.cpp, teensy_dsc.h]
2015-05-09 update test.py
    - print stats on Ctrl-C
    - count number of times we exceed warning level (default 0.3sec)
    - be more accurate on calc avg based on actual run time
2015-05-10 Update COMMANDS.md & clean up cli.cpp
    - Add/fix missing commands
    - Optimize cli commands a little
    [cli.cpp]
2015-05-10 refs: #41 include all the libraries we need.
    This doesn't currently auto-import them into the Arduino.app
    or anything like that (you still need to manually import them)
    but at least you don't have to go looking for them & download
    them one by one.
2015-05-12 refactor code to make it easier to unit test
    - move key method to it's own dsc.[h|ino]
    - remove same method from unit_tests.ino
    - Makefile to copy necessary files
    Use Arduino tool to compile/run unit tests
2015-05-14 Teensyduino includes the MsTimer2 library
2015-05-24 switch Flash to use my fork
2015-05-24 Update with pull request to fix Arduino 1.5.x support
    https://github.com/mikalhart/Flash/pull/5
2015-09-20 Only the AstroDevices Nexus is really similar to the TeensyDSC
2017-06-30 Fix negative encoder range
    So if you install your encoder on the "other" side, you need
    to configure it as a negative resolution. The old code handled
    this very badly and effectively returned really bad results if
    you configured a negative resolution.
    We also write a bunch of unit tests to validate the values are now
    correct.
    [dsc.ino, teensy_dsc.ino, unit_tests.ino]
2017-07-04 Fix negative resolution support
    Negative resolution was totally broken! Fix support and write a
    bunch of test cases proving it works.
    One little problem... the negative 10K tests don't work reliably??? WTF?
    They work just fine on their own, but don't work when other tests are
    run. No idea why?
    Fixes #46
    [dsc.ino, unit_tests.ino]
2017-07-09 Don't double negative
    So when an encoder resolution is negative, I was reversing the
    result returned to the DSC. This is *WRONG*. The DSC is supposed to
    do the needful when the resolution is negative. This caused a problem
    (usually for Alt encoders) whereby up was down and down was up when the
    resolution is negative.
    We now cacluate the value to return to the DSC the same regardless of
    if the resolution is positive or negative and let the DSC do the right
    thing.
    fixes: #46
    [dsc.ino, unit_tests.ino]
2018-05-02 replace bzero with memset
    fixes compile under Arduino IDE 1.8.5
    [cli.cpp]

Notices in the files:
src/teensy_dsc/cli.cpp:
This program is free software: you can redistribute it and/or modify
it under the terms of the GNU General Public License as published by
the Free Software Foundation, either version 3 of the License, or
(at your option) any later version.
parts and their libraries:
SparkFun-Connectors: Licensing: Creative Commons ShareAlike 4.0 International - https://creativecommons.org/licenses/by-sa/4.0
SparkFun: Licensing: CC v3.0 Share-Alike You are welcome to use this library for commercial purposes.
